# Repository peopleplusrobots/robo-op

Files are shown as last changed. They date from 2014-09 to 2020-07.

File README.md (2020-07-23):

## Robo.Op
### Industrial Robots. Open for Creativity.

_Robo.Op_ is an open hardware / open software platform for hacking industrial robots (IRs). 
_Robo.Op_ makes it cheaper and easier to customize your IR for creative use, so you can _explore the fringes of industrial robotics_.
<br/><br/>
_See [this](https://github.com/peopleplusrobots/robo-op/wiki/3.-Software:-Getting-Started-Tutorial) tutorial to get started._
<br/><br/>
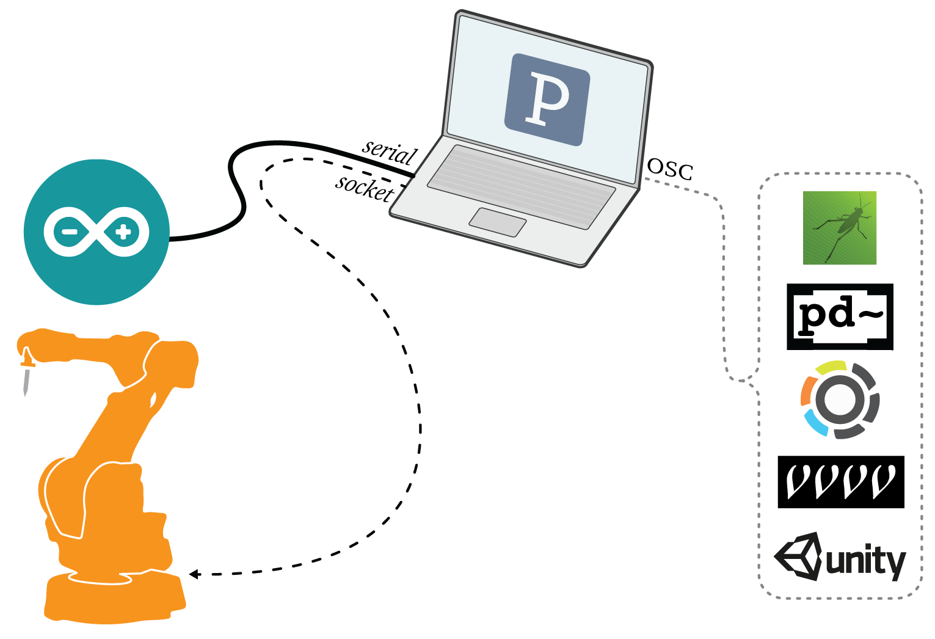
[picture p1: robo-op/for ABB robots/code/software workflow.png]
Software Workflow

<br/><br/>
We built _Robo.Op_ to bypass the expensive, proprietary software and hardware currently offered by robotics companies. _Robo.Op_ enables artists and designers to _(a)_ develop affordable custom tools for creative robotics, and _(b)_ share tools and knowledge across robotic platforms.
<br/><br/>
_Robo.Op_ is made of three components:<br/>
<ul>
<li>The Robot Tool Adaptor (RTA) – a universal adaptor sheild for developing affordable, custom tools for creative robotics.</li>
<li>A Processing Interface – a simplified, modular software interface for cross-platform programming of IRs.</li>
<li>A Centralized Knowledge Hub - this github-hosted project for sharing knowledge, tools, and code.</li>
</ul>

> The full Project Overview can be found [here](https://github.com/peopleplusrobots/robo-op/wiki/1.-Project-Overview).

#### Opening Hardware
For tutorials on adapting, fabricating, & assembling your RTA, click [here](https://github.com/peopleplusrobots/robo-op/wiki/2.-Hardware:-Design,-Fabrication-&-Assembly).

To download the RTA fabrication files, click [here](https://github.com/peopleplusrobots/robo-op/tree/master/robo-op/for%20ABB%20robots/fabrication%20files).

#### Opening Software
For tutorials for using our Processing Interface to control your IR, click [here](https://github.com/peopleplusrobots/robo-op/wiki/3.-Software:-Workflow-&-Integration).

To download the code, click [here](https://github.com/peopleplusrobots/robo-op/tree/master/robo-op/for%20ABB%20robots/code).

#### Sharing Knowledge
Visit the [wiki](https://github.com/peopleplusrobots/robo-op/wiki) for resources related to *Robo.Op* and creative robotics.

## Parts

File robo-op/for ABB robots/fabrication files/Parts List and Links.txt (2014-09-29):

T-Slot:  http://www.mcmaster.com/#t-slotted-hanging-track/=tx0f2r

Mil Spec Connectors: http://www.mcmaster.com/#mil.-spec.-pin-and-socket-connectors/=tx0qmi

Electric Receptacles: http://www.mcmaster.com/#nema-receptacles/=tx0rou

Acrylic Weld: http://www.eplastics.com/PLEXIGLASS-GLUE-ADHESIVE-IPS-4-4OZ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

Stack Headers: https://www.sparkfun.com/products/10007

MicroController:  http://store.arduino.cc ;  https://www.sparkfun.com/products/12757

Xbee Shield for Microcontroller: https://www.sparkfun.com/products/12847

Xbee Explorer: https://www.sparkfun.com/products/11697

Xbee RF Modules: http://www.digi.com/products/wireless-wired-embedded-solutions/zigbee-rf-modules/

Acrylic: This item can often be purchased locally.  It is important to know actual dimensions of thickness as it may effect the width of adjacent parts.  The original model uses one sheet of .22" (6mm) and one sheet .117" (3mm) acrylic.

Circuit board:  A generic example is included in the voltage conversion (VC) pin mapping diagram describing signal out from robot to VC, VC to microcontroller, microcontroller to VC and VC to robot.

Circuity components:

Pin Mapping: Low Voltage:  Please see your industrial robot controller documents for a list of available low-voltage (signal) connections (Examples of the original configuration are included, but only to reference the type of document you'll need to map connections). It is not possible to describe exactly what connections one will have available, and therefore which robot signal pins need to connect to microcontroller signal pins.  

Pin Mapping: High Voltage:  Please see your industrial robot controller documents for a list of available high-voltage power connections (Examples of the original configuration are included, but only to reference the type of document you'll need to map connections). It is not possible to describe exactly what connections one will have available, and therefore which robot signal power need to connect to power receptacle pins.

Assembly: Current version is mainly adhered with acrylic weld.  The pieces containing the aluminum track are stacked 2 deep in addition to the outside plate (total 3 layers of .22"(6mm).  The covers for enclosures B and D (high voltage) can be attached in various ways.  We chose to drill, tap and screw them in for safety.  It is imperative that the electric receptacle enclosures be safely sealed from human contact.

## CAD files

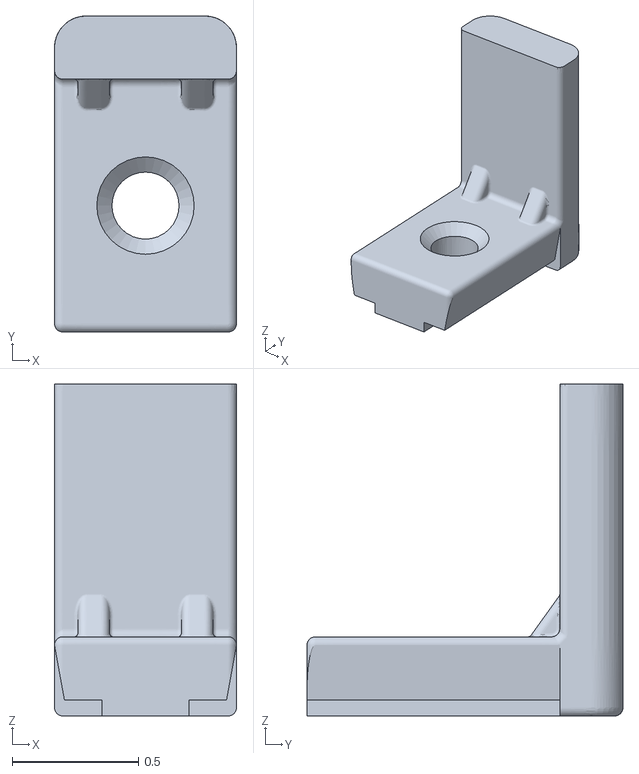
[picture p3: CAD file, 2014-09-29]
robo-op/for ABB robots/fabrication files/RTA Attachments/mountBase.stl
0.72 x 1.25 x 1.31

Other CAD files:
robo-op/for ABB robots/fabrication files/RTA Assembly/RTA_thin_laser.dxf
robo-op/for ABB robots/fabrication files/RTA Assembly/RTA_thick_laser.dxf

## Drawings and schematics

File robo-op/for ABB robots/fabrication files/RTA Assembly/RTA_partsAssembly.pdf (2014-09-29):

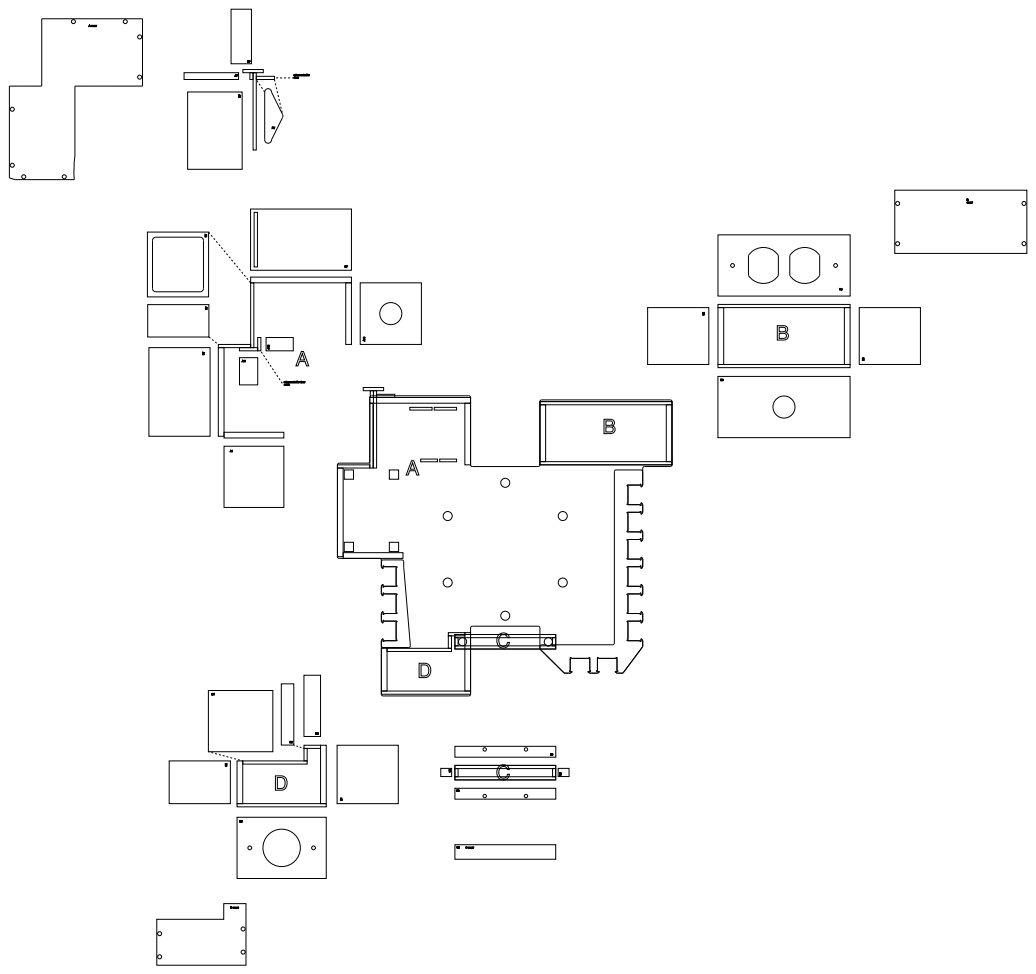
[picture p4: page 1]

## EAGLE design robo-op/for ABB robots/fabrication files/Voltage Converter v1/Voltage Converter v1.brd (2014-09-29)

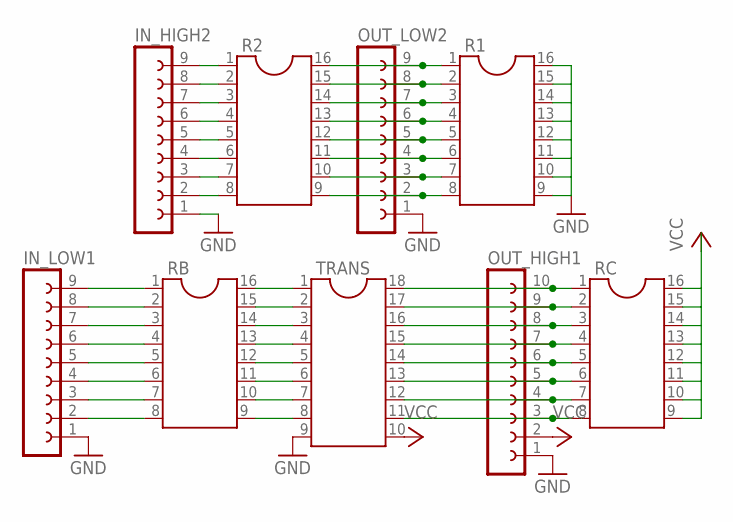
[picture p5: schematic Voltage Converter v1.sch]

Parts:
IN_HIGH2: FE09-1; FE09
IN_LOW1: FE09-1; FE09
OUT_HIGH1: FE10-1; FE10
OUT_LOW2: FE09-1; FE09
R1, R2: DIL16S; SOCKET-16
RB: DIL16S; SOCKET-16
RC: DIL16S; SOCKET-16
TRANS: DIL18S; SOCKET-18

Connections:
GND: IN_HIGH2.1, IN_LOW1.1, OUT_HIGH1.1, OUT_LOW2.1, R1.9, R1.10, R1.11, R1.12, R1.13, R1.14, R1.15, R1.16, TRANS.9
unnamed: IN_LOW1.2, RB.8
unnamed: IN_LOW1.3, RB.7
unnamed: IN_LOW1.4, RB.6
unnamed: IN_LOW1.5, RB.5
unnamed: IN_LOW1.6, RB.4
unnamed: IN_LOW1.7, RB.3
unnamed: IN_LOW1.8, RB.2
unnamed: IN_LOW1.9, RB.1
unnamed: RB.9, TRANS.8
unnamed: RB.10, TRANS.7
unnamed: RB.11, TRANS.6
unnamed: RB.12, TRANS.5
unnamed: RB.13, TRANS.4
unnamed: RB.14, TRANS.3
unnamed: RB.15, TRANS.2
unnamed: RB.16, TRANS.1
unnamed: OUT_HIGH1.10, RC.1, TRANS.18
unnamed: OUT_HIGH1.9, RC.2, TRANS.17
unnamed: OUT_HIGH1.8, RC.3, TRANS.16
unnamed: OUT_HIGH1.7, RC.4, TRANS.15
unnamed: OUT_HIGH1.6, RC.5, TRANS.14
unnamed: OUT_HIGH1.5, RC.6, TRANS.13
unnamed: OUT_HIGH1.4, RC.7, TRANS.12
unnamed: OUT_HIGH1.3, RC.8, TRANS.11
unnamed: IN_HIGH2.2, R2.8
unnamed: IN_HIGH2.3, R2.7
unnamed: IN_HIGH2.4, R2.6
unnamed: IN_HIGH2.5, R2.5
unnamed: IN_HIGH2.6, R2.4
unnamed: IN_HIGH2.7, R2.3
unnamed: IN_HIGH2.8, R2.2
unnamed: IN_HIGH2.9, R2.1
unnamed: OUT_LOW2.9, R1.1, R2.16
unnamed: OUT_LOW2.8, R1.2, R2.15
unnamed: OUT_LOW2.7, R1.3, R2.14
unnamed: OUT_LOW2.6, R1.4, R2.13
unnamed: OUT_LOW2.5, R1.5, R2.12
unnamed: OUT_LOW2.4, R1.6, R2.11
unnamed: OUT_LOW2.3, R1.7, R2.10
unnamed: OUT_LOW2.2, R1.8, R2.9
VCC: OUT_HIGH1.2, RC.9, RC.10, RC.11, RC.12, RC.13, RC.14, RC.15, RC.16, TRANS.10

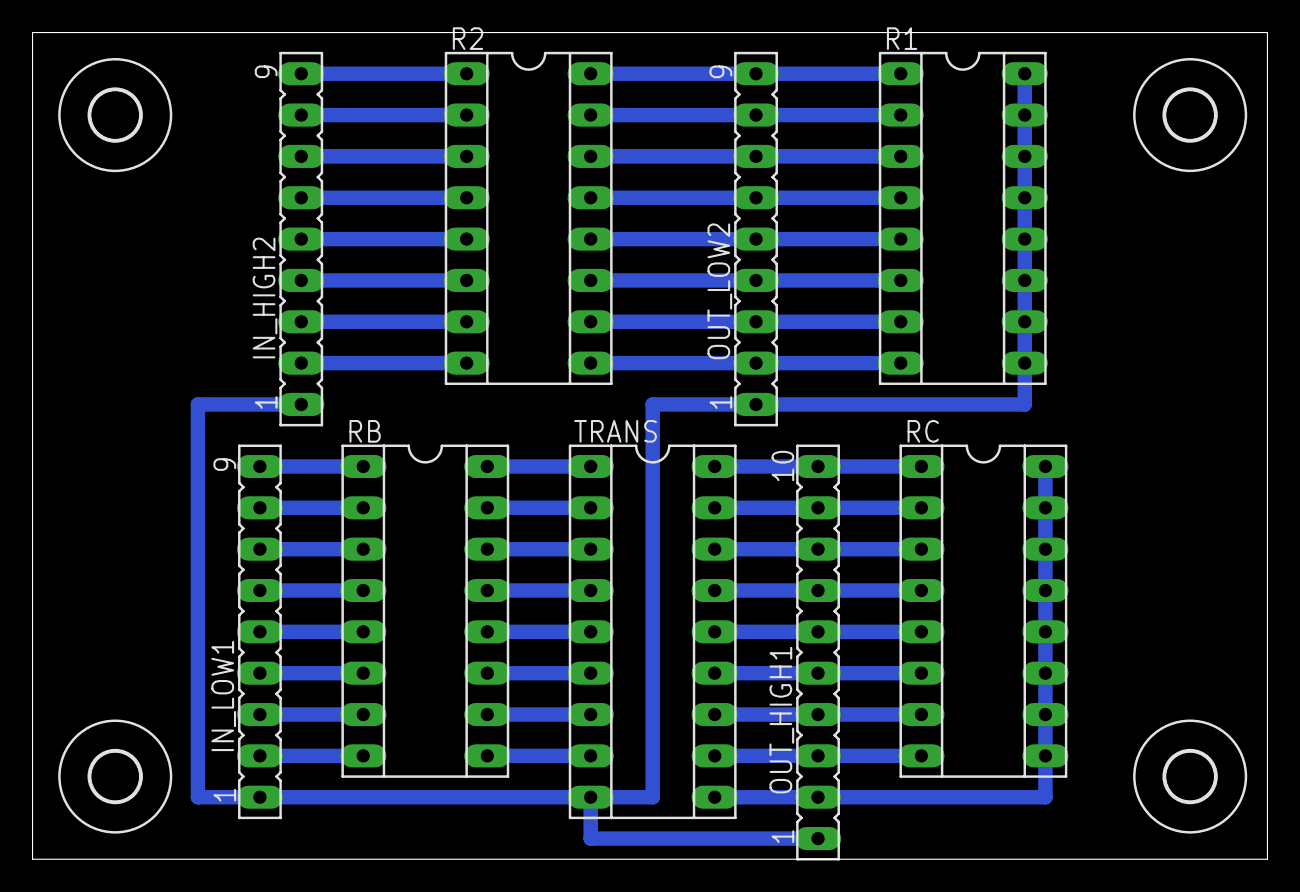
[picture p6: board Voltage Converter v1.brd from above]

Board: 2 copper layers, 75.9 x 50.8 mm, 13 parts (0 on the bottom side), 42 nets.

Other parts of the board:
U$1, U$2, U$3, U$4: 3,0

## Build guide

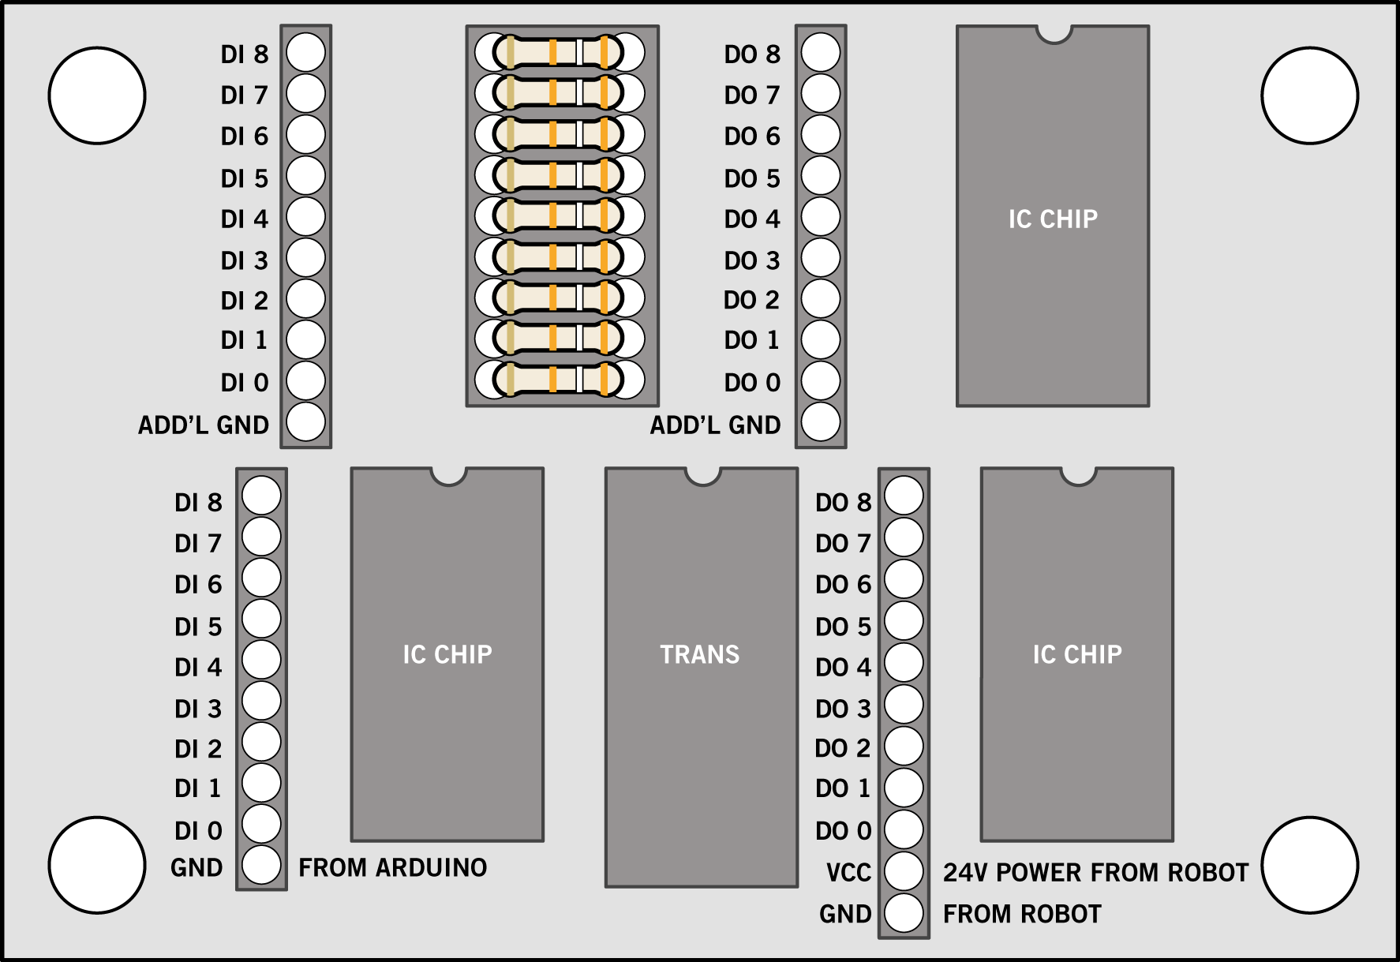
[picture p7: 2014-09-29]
robo-op/for ABB robots/fabrication files/Voltage Converter v1/robo-op_Voltage Converter Diagram.png

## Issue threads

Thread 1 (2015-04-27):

Reg. Software Workflow

CaptainMack, 2015-04-27:
Hi!

I love the idea behind the project, but I've noticed that there's not really any information in: https://github.com/peopleplusrobots/robo-op/wiki/3.-Software:-Workflow-&-Integration

I am also guilty of having too many things on my table, so I won't stress about it - I simply need a few details for getting the Arduino->Processing->Robot communication software to work.

//Chris

zackjw, 2015-05-01:
Hi Chris,

Thank you for getting in touch.  I'm copying Madeline and Mike here as they've been refining that workflow since October.  I'm no longer in the same lab as them and, regardless, I had less to do with the software pipeline and more to do with design and fabrication of the object itself.

Hopefully they can get you what you need.  Should be, roughly, an Arduino/Xbee > Java > Grasshopper(Rhino3D)> ABB Controller/IP address flow.

Please keep in contact.  We're thrilled to hear that someone's appropriating the project!

Best,
Zack
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

madelinegannon, 2015-05-20:
Hi Chris,

Thanks for your patience ... I've uploaded a new _Getting Started Tutorial_ [here](https://github.com/peopleplusrobots/robo-op/wiki/3.-Software:-Getting-Started-Tutorial) and some more advanced (but messy!) example projects [here](https://github.com/peopleplusrobots/robo-op/wiki/4.-Example-Projects).

Let us know how it goes!

-Madeline

Closed 2015-10-02.

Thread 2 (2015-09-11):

LAN connection

compmonks, 2015-09-11:

zackjw, 2015-09-11:
Hi Pierre, we had the same problem at the university and, unofficially, had to find a creative solution.  Unofficially ;)

I’ve copied Madeline and Mike Jeffers here who are both still working at dFab and can tell you what protocol they’ve used since then.  It could involve a de facto ‘hacking’ of your system.  We called it “research”.

Best,
Zack
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

madelinegannon, 2015-09-11:
Hi Pierre,

We just plugged our LAN connection into a wifi router and created a local network (an intranet, I guess).

compmonks, 2015-09-11:
Hi Zack, thanks.
I was actually closing the issue because by doing a quick  "research" scanning of listening ports (currently 139) I could manage to establish a connection. The Getting started applet works fine but
commands does not seem to be read....

compmonks, 2015-09-24:
ok, I finally got a working LAN version.
Even though you mentionned it, I had to explicit a few steps in order to reproduce the connection procedure with the students :

for the module:
#####################
! Working version for LAN connections
! Tips: - Robot IP can be checked in TeachPendant Menu
!                                     >System Info
!                                      >Controller Properties
!                                       >Network Connection
!                                        >LAN
!       - Make Sure the computer is in the same subnet (if the controller IP is 192.168.133.2, then the computer IP should be 192.168.133.20 for example)
!       	- Go to your Network and Connection menu (in Windows: Network and Sharing Center)
!			- Click on the Local Area Connection you are using then 'Properties' > 'Internet Protocol Version 4' (TCP/Ipv4) > 'Properties'
!			- Select 'Use the following IP Adress' (Fixed IP) and type the corresponding IP (192.168.133.20 in this example)
!           - Do not forget to add as well the subnet mask and default gateway. Exactly the same than the Controller.
#####################

 for the Processing Applet file :
#####################

* WORKING VERSION FOR LAN CONNECTION
 * QUICK TIP :
 * - After loading the newly configured MOD file, in the TeachPendant menu, go to 'Production Window' > 'PP To Main' and then press the Play button
 * - Make sure motors are 'ON' on the controller side and it is set to 'AUTOMATIC' mode

#####################

All the best :)
Pierre

madelinegannon, 2015-10-02:
Hi Pierre,

Thanks for posting your LAN configuration!

For safety reasons, we *strongly* recommend running in MANUAL mode, not full Automatic.
Manual mode runs slower and someone will have to be hold down the deadman switch on the teach pendant. But unpredictable movements can happen when streaming commands, and manual mode can help minimize this risk.

We are looking forward to seeing what you make!

–Madeline

Closed 2015-10-02.

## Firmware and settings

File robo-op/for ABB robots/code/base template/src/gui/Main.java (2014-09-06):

package gui;

import java.applet.Applet;
import java.awt.Dimension;
import java.awt.FlowLayout;
import java.awt.Frame;
import java.awt.event.WindowAdapter;
import java.awt.event.WindowEvent;

/**
 * The Main class allows you to have multiple PApplets in one application. <br/>
 * Run this class to start your application.
 * 
 * @author mad
 */
public class Main extends Frame{
	
	public Main(){
		super("R0BOT Ð Template File");
		
		//get display screen size for Frame sizing
		Dimension screenSize = java.awt.Toolkit.getDefaultToolkit().getScreenSize();
		Dimension preferredSize = new Dimension(screenSize.width/2, screenSize.height/2);

		this.setResizable(true);
		this.setPreferredSize(preferredSize);
		this.setMaximumSize(screenSize);
		this.setMinimumSize(preferredSize);

		// instantiate the Applet
		final Applet gui = new GUI(this); 

		// add the applet to the frame
		this.add(gui,FlowLayout.LEFT);		

		// closes application 
		addWindowListener(new WindowAdapter() {
			public void windowClosing(WindowEvent e) {
				System.exit(0);
			} });


		// get threads synchronized
		gui.init();
		
	}
	

	public static void main(String[] s){
		new Main().setVisible(true);		
	}

}

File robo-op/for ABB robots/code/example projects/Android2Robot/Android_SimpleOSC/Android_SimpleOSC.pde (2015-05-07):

import oscP5.*;
import netP5.*;

import android.view.MotionEvent;

import ketai.ui.*;

/**
 * Simple_OSC
 * A simple drawing app that sends points  
 * and curves to a Processing sketch via OSC.
 *
 * Touch & Drag to draw
 * Double Tap to clear the canvas
 *
 * @mad
 * 2.13.2015
 */


OscP5 oscP5;
NetAddress myRemoteLocation;

KetaiGesture gesture;

/**
 * In drawMode, the app sends over curves, not individual points.
 */
boolean drawMode = true;   
boolean tap = false;
boolean clear = false;

int mx = 0;
int my = 0;
int phoneWidth = 0;
int phoneHeight = 0;

private static final String IP_remote = "128.2.109.103";   // your computer's IP addr
private static final int PORT = 12000;

PVector touchPt = new PVector();
ArrayList<ArrayList<PVector>> ptList = new ArrayList<ArrayList<PVector>>();
ArrayList<PVector> pts = new ArrayList<PVector>();

void setup() {
  size(displayWidth, displayHeight);
  background(220);

  textSize(32);
  textAlign(CENTER);

  phoneWidth = displayWidth;
  phoneHeight = displayHeight;
  orientation(LANDSCAPE);

  // set up gesture detection
  gesture = new KetaiGesture(this);  

  // set up communication
  oscP5 = new OscP5(this, PORT);
  myRemoteLocation = new NetAddress(IP_remote, PORT);

  // send our screen dimensions
  OscMessage setup = new OscMessage("/setup");
  setup.add(phoneWidth);
  setup.add(phoneHeight);
  oscP5.send(setup, myRemoteLocation);
}


void draw() {
  background(60);
  smooth();

  if (drawMode) {

    pushStyle();
    noFill();
    strokeWeight(10);
    stroke(255, 0, 255);

    // visualize current curve
    beginShape();
    for (int i=0; i<pts.size (); i++)
      vertex(pts.get(i).x, pts.get(i).y);  
    endShape();

    // visualize past curves
    for (int i=0; i<ptList.size (); i++) {
      ArrayList<PVector> list = ptList.get(i);
      beginShape();
      for (int j=0; j<list.size (); j++) 
        vertex(list.get(j).x, list.get(j).y);
      endShape();
    }    
    popStyle();

    /* clear the canvas on double tap */
    if (clear){

      // send a 'clear canvas' bang
      OscMessage myMessage = new OscMessage("/clear");
      myMessage.add("clear");
      oscP5.send(myMessage, myRemoteLocation);
  
      // clear our lists
      pts.clear();
      ptList.clear(); 
      
      clear = false; 
    }
  }
  // draw cross-hairs for touch point
  else if (!drawMode ) {
    pushStyle();
    noFill();
    strokeWeight(25);
    stroke(200);
    line(0, touchPt.y, width, touchPt.y);
    line(touchPt.x, 0, touchPt.x, height);
    rectMode(CENTER);
    strokeWeight(15);
    stroke(180);
    rect(touchPt.x, touchPt.y, 100, 100);
    popStyle();
  }
}

void mouseDragged() {

  /* Record touches, if we're not tapping */
  if (tap) {
    tap = false;
  }
  // if we're not tapping the screen
  else {

    // add the mouse to our pt list
    pts.add(new PVector(mouseX, mouseY));

    touchPt.x = mouseX;  
    touchPt.y = mouseY; 

    // send invidual points if we're NOT drawing curves
    if (!drawMode) {
      ArrayList<String> msg = new ArrayList<String>();
      msg.add("{"+mouseX+", "+mouseY+", 0}");
      sendPts(msg);
    }
  }
}

void mouseReleased() {

  tap = true;

  OscMessage myMessage = new OscMessage("/point");

  ArrayList<PVector> temp = new ArrayList<PVector>();
  for (PVector p : pts) {
    temp.add(p);
    myMessage.add(p.toString());
  }

  if (drawMode && temp.size()>2)
    oscP5.send(myMessage, myRemoteLocation); 

  ptList.add(temp);
  pts.clear();
}

void sendPts(ArrayList<String> pts) {
  OscMessage myMessage = new OscMessage("/point");
  for (String s : pts)
    myMessage.add(s);
  oscP5.send(myMessage, myRemoteLocation);
}

/* incoming osc message are forwarded to the oscEvent method. */
void oscEvent(OscMessage theOscMessage) {
  /* print the address pattern and the typetag of the received OscMessage */
  print("### received an osc message.");
  print(" addrpattern: "+theOscMessage.addrPattern());
  println(" typetag: "+theOscMessage.typetag());
}

void onDoubleTap(float x, float y) {
  tap = true;

  clear = true;
}

/**
 * Use 'tap' for debouncing ... so we don't add extra unwanted points. 
 */
void onTap(float x, float y) {
  tap = true;
}

public boolean surfaceTouchEvent(MotionEvent event) {

  //call to keep mouseX, mouseY, etc updated
  super.surfaceTouchEvent(event);

  //forward event to class for processing
  return gesture.surfaceTouchEvent(event);
}

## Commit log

2014-09-25 changed Arduino class to Serial class
2014-09-29 added fabrication files
    [Voltage Converter v1.brd, Voltage Converter v1.sch]
2014-09-29 added assembly and cut files
    [RTA_thick_laser.dxf, RTA_thin_laser.dxf, mountBase.stl]
2014-10-07 organized repo and cleaned up template code
    [RTA_thick_laser.dxf, RTA_thin_laser.dxf, Voltage Converter v1.brd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]
